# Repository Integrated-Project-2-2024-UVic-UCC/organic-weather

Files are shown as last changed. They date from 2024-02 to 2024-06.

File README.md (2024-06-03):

#  ORGANIC WEATHER STATION
The "Organic Weather Station" blends botanical aesthetics with robotics, creating a responsive flower-like robot. Equipped with photodiodes, a stepper motor, and an ESP32, this design emulates the natural behavior of flower petals that open and close with changes in light levels. It demonstrates a harmonious integration of components, providing both environmental feedback and decorative value in indoor settings.

## Features
- **Adaptive Petal Movement**:  Responds to light intensity data from photodiodes, controlling the movement of its petals to mimic natural responses.
- **Environmental Feedback**: Responds to light intensity data from photodiodes, controlling the movement of its petals to mimic natural responses.
- **Remote Weather Updates**: Connects with a Telegram chat to retrieve and display weather conditions from any specified location.
- **Ambient LED Effects**: Incorporates LEDs within the petals that shift colors based on the ambient room temperature.

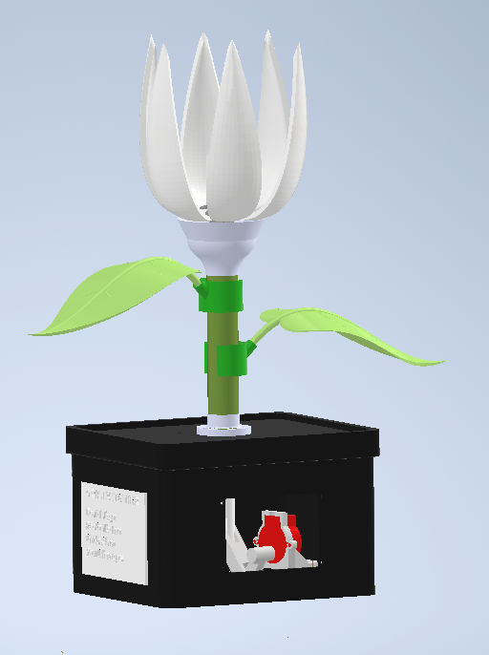
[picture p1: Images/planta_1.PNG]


If you are interested in carrying out this project, we invite you to the following sections!

## README STRUCTURE
- [Promotional Video](#promotional-video)
- [Materials](#materials)
- [Mechanical part](#mechanical-part)
    - [ 3D printed parts](#3d-printed-parts)
    - [Hardware parts](#hardware-parts)
- [Electrical Part](#electrical-part)
    - [Datasheets](#datasheets)
    - [Electric scheme](#electric-scheme)
- [Programming Part](#programming-part)

## PROMOTIONAL VIDEO
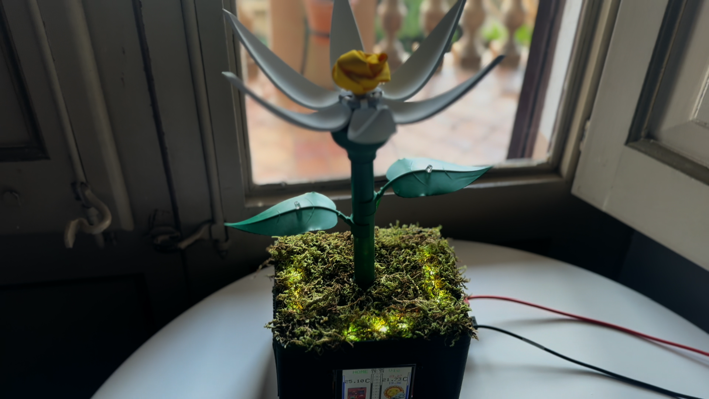
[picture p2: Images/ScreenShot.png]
Video Screenshot

[Promotional video](https://github.com/Integrated-Project-2-2024-UVic-UCC/organic-weather/blob/main/Images/OrganicWeather_PromotionalVideo.mp4)
## MATERIALS
Before starting with the mechanical part, we will show you the list of materials that have been used and the links where you can buy it:
|Component|Description|Link|Price (€)|
|---|---|---|---|
| |ESP32-DEVKITC-32UE, MAIN SHIELD |(https://www.digikey.es/es/products/detail/espressif-systems/ESP32-DEVKITC-32UE/12091813) |9,23 €|
| |TFT LCD 3.2″ 240×320 RGB SPI Display with Touchscreen| https://protosupplies.com/product/tft-lcd-3-2-240x320-rgb-spi-display-with-touchscreen/ | 17,7 €|
| |Stepper motor 28BYJ-48 (5V) with ULN2003 driver|https://tienda.bricogeek.com/motores-paso-a-paso/969-motor-paso-a-paso-28byj-48-5v-con-driver-uln2003.html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 | 2,95 €|
| | DHT22 humidity and temperature sensor| https://eu.robotshop.com/es/products/dht22-temperature-humidity-sensor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 | 7,49 €|
| | SFH 203 P Photodiode | https://www.digikey.es/es/products/detail/ams-osram-usa-inc/SFH-203-P/1893875 | 1 - 0,92 € |
| |WS2812B Module Circuit with RGB Led| https://www.shoptronica.com/led-bicolor-tricolor-rgb/3959-circuito-modulo-ws2812b-con-led-rgb-0689593949912.html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 | 1 - 0,2610 €|

The datasheets for these components can be found in the following folder: [Datasheets](https://github.com/Integrated-Project-2-2024-UVic-UCC/organic-weather/tree/main/Electronic/Datasheets)

## MECHANICAL PART
  ### 3D printed parts

After reviewing the description of the organic weather station and understanding its required functions and movements, this section will explain the mechanisms used to ensure the flowers open and close correctly each time.
Flower mechanism
As a first option, it was proposed to move the petals using four gears, each connected to a petal, and a worm gear in the center, connected to the motor. This mechanism was to allow the petals to open and close depending on the light intensity of the environment. The worm gear turned and had to engage with the gears to make them rotate, which worked in the simulation. However, when printed, the system generated too much friction, which caused constant breakage and malfunction. Because of these friction and unreliability problems, the design was eventually discarded.
After this, a new design was started. This innovative design does not have gears or worm gear, in short, it has two pieces without considering the petals. The first piece will be a central piece, one end of which will be connected to the stepper motor that will carry out the movement and the other part is where the petals will be hooked. This part will be like a crown where the petals will be placed, that is, they will fit together, allowing the petal to have complete movement. We could imagine the movement as that of a hinge. The second piece will be both functional and visual. We can see that visually it will be a calyx of a flower and inside it will have the shape of a coup. Its function will be that when the central piece lowers, the petals, when resting on the calyx, begin to close on the inside of the cup, so when the central piece has reached its minimum, the flower is completely closed. 

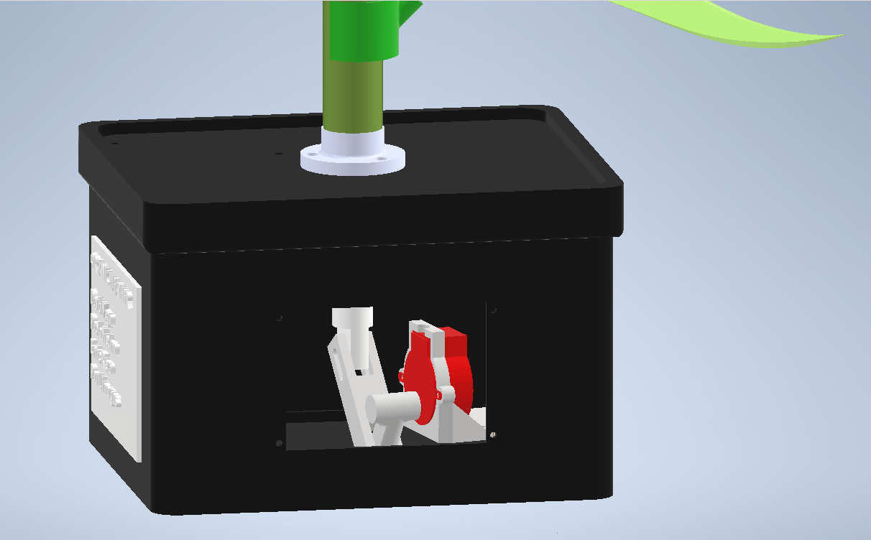
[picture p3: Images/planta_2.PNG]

|Component|Description|3D part|
|---|---|---|
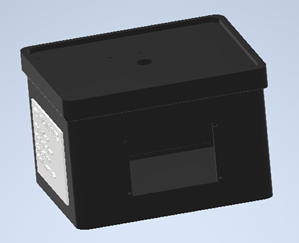
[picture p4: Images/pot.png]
| POT | Pot of the plant, inside it has all the electronic components |  |
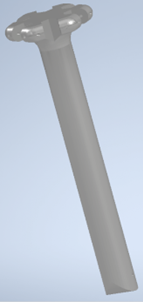
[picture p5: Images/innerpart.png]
| INNER PART | The Main bar, to move the petals of the flower, is connected to the stepper motor | |
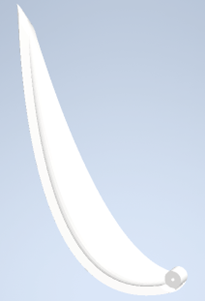
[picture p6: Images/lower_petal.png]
| FLOWER PETAL | Six of these complete the flower, with the hinge on the bottom it connects to the Inner Part, to be able to open and close |  |
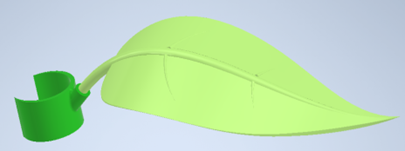
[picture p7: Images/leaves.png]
| LEAVES | The greener is the support of the leaf that it is attached to the stem of the plant. We have two, one on each side, the left and the right. |  |

These are the parts of the mechanism inside the pot, that we use:

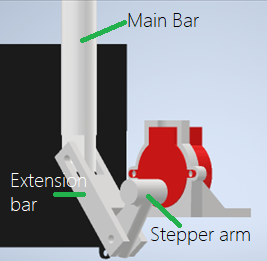
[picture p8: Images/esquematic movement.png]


  ### Hardware parts
  
## ELECTRICAL PART
  ### Datasheets
  You can find the datasheets for the following components in the [datasheets folder](https://github.com/Integrated-Project-2-2024-UVic-UCC/organic-weather/tree/main/Electronic/Datasheets):
  - ESP32
  - Photodiodes
  - LEDs RGB
  - DHT22 humidity and temperature sensor
  ### Electric scheme
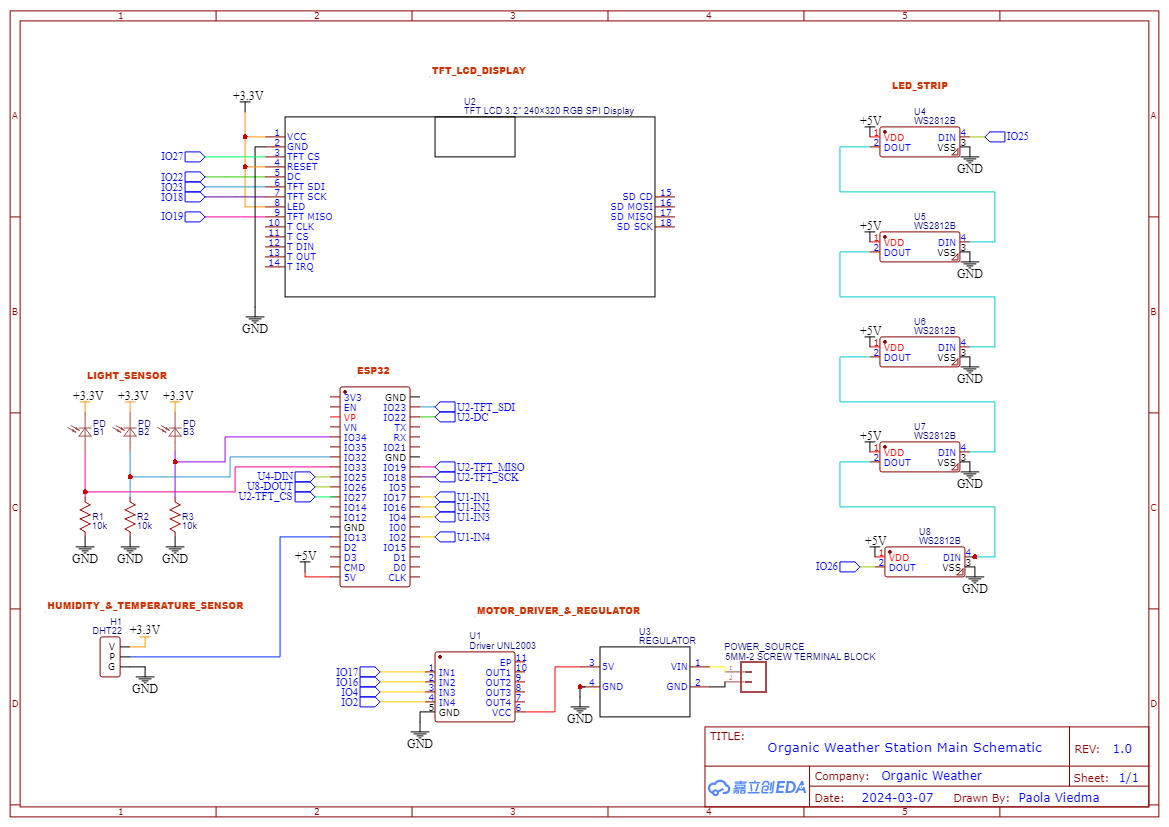
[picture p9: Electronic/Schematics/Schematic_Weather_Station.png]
Schematic_Weather_Station
  )
  [![Electric Scheme]([https://github.com/Integrated-Project-2-2024-UVic-UCC/organic-weather/blob/main/Electronic/Schematics/Schematic_Weather_Station.png](https://github.com/Integrated-Project-2-2024-UVic-UCC/organic-weather/blob/main/Electronic/Schematics/Schematic_Integrated%20Project_2024-04-24.png))](https://github.com/Integrated-Project-2-2024-UVic-UCC/organic-weather/tree/main/Electronic/Schematics)

## PROGRAMMING PART
The libraries used are located in the Code folder, as a folder called LIBRARIES. 
Here is explained synthesized the main workflow of the code. 

### Workflow of the HTTP Client 
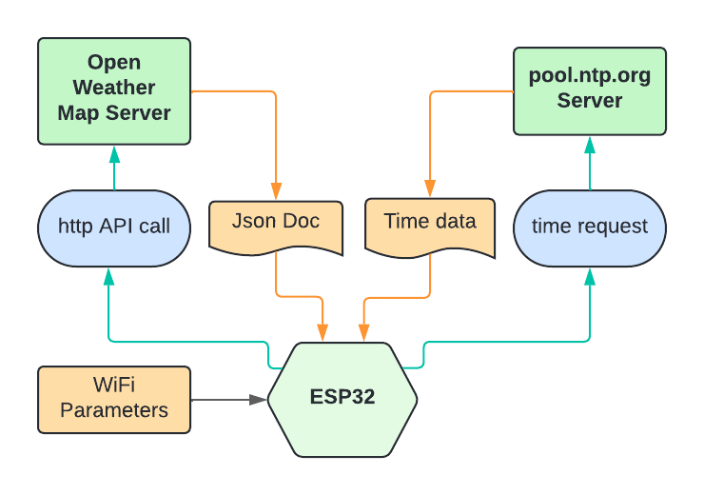
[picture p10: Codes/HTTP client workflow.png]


### Global/Loop workflow 
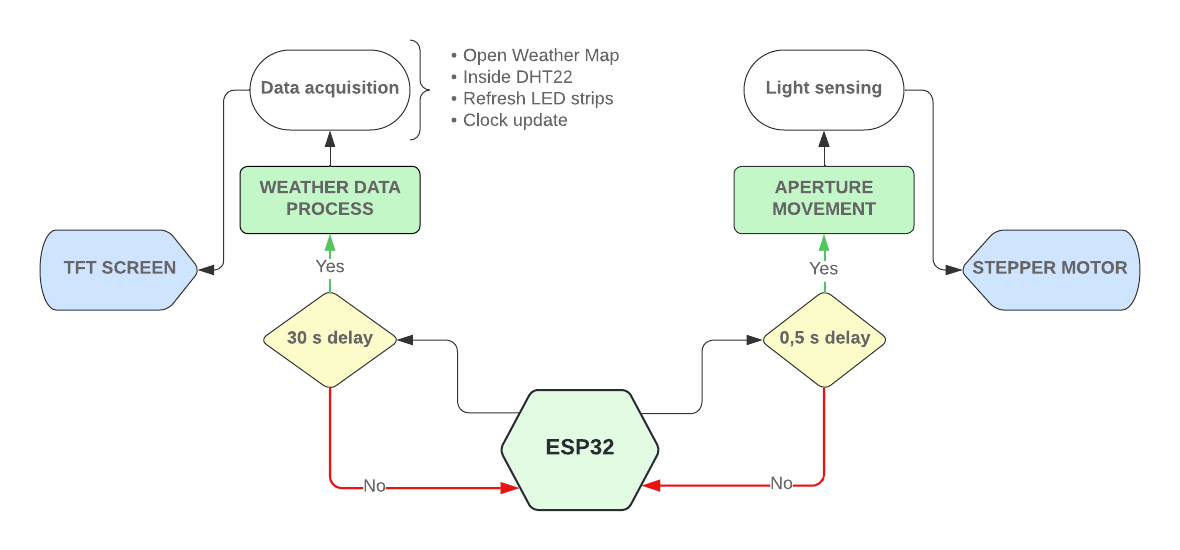
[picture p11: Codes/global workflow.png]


### Setup
For inicialize the plant:
- Starts the screen with the welcome screen
- Reset the position of the stepper motor
- Starts the WiFi connection
- Configure the Real Time Clock of the ESP32
- Do a first run of two main processes
  - Light sensing and motor position
  - Data adquire and data display

### Loop
When the system has been started up correctly, the main loop only execute two subprocesses:
- Light sensing and motor position
- Data aquire and data display
  
This two subprocesses have diferent delay time, controlled by comparison of the millis() function.
For the aperture of the leaves needs a fast frequency, is set to 0,5 seconds.
For the data aquire and data display doesn't need a high frequency because the data may not vary significantly. The delay is set to 30 seconds.

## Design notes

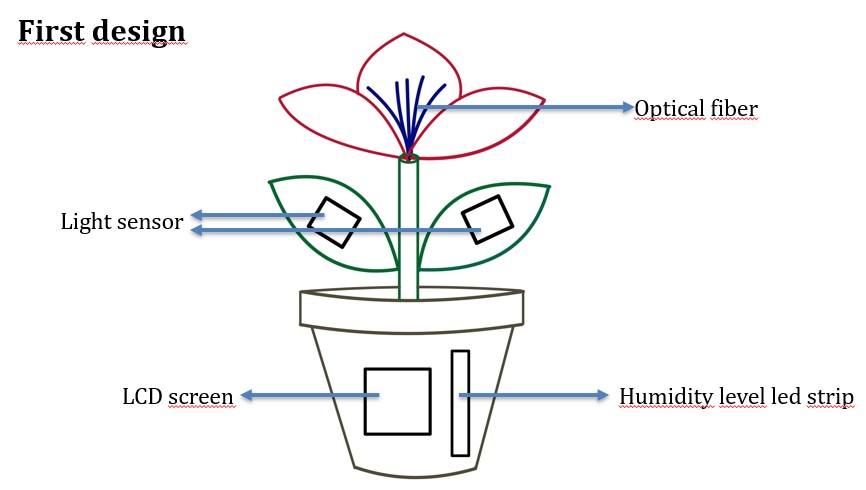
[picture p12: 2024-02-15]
Images/first_design.jpg

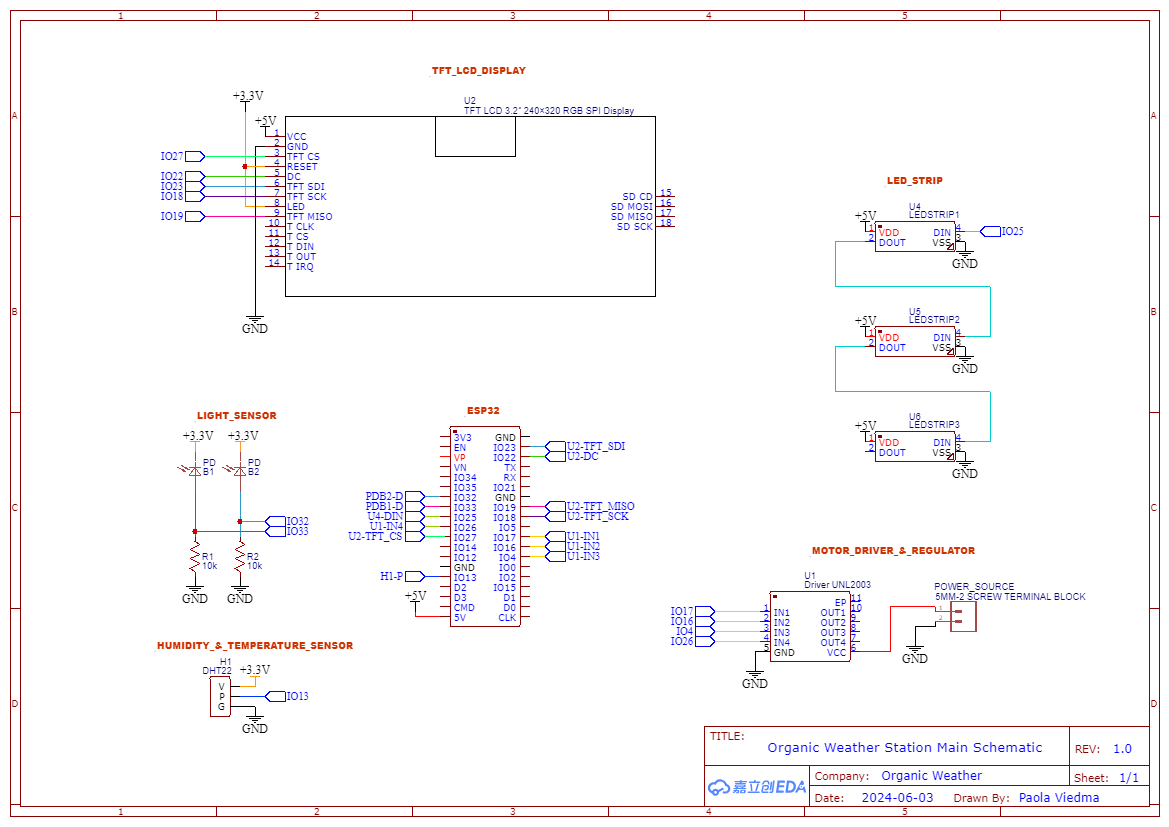
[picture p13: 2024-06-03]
Electronic/Schematics/Schematic_Integrated Project_2024-06-03.png

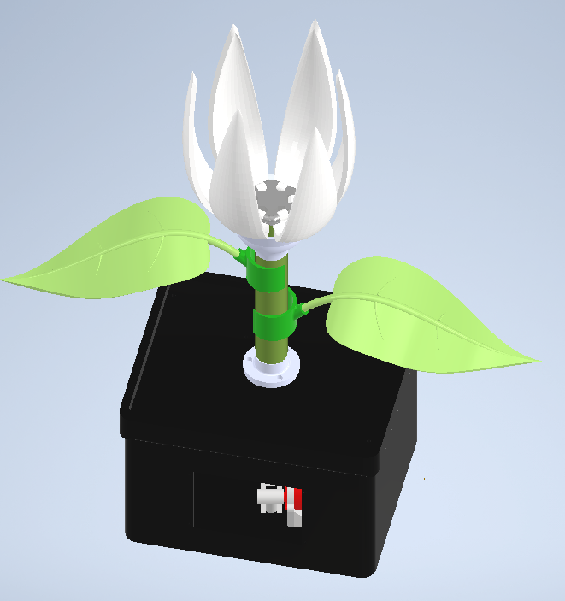
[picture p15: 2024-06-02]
Images/planta_4.PNG

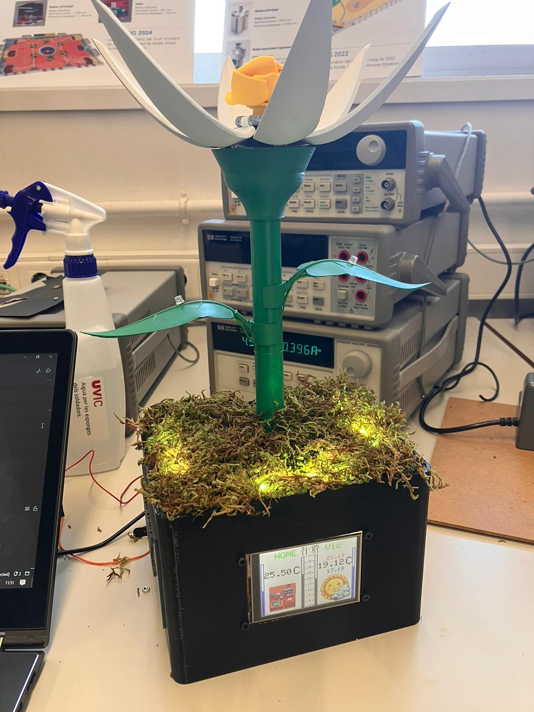
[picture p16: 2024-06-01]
Images/final_prototype.jpg

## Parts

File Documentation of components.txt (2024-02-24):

Arduino nano ble
14 I/O

The power supply will come directly from the battery, with the pins Vin and GND that supports a top of 21 V.
The converter 12V to 5V will supply the servomotor. 
It will be possible that this converter feeds the LEDs and the fiberoptic.

Outputs: 
	1 PWM servomotor control
	3 PWM for the control of the three colors of RGB LEDs termometer
	1 of tqhe fiberoptics

I2C:
	DHT22 temp and hum
	OLED Display

Inputs:
	3 analog inputs from the photoresistor

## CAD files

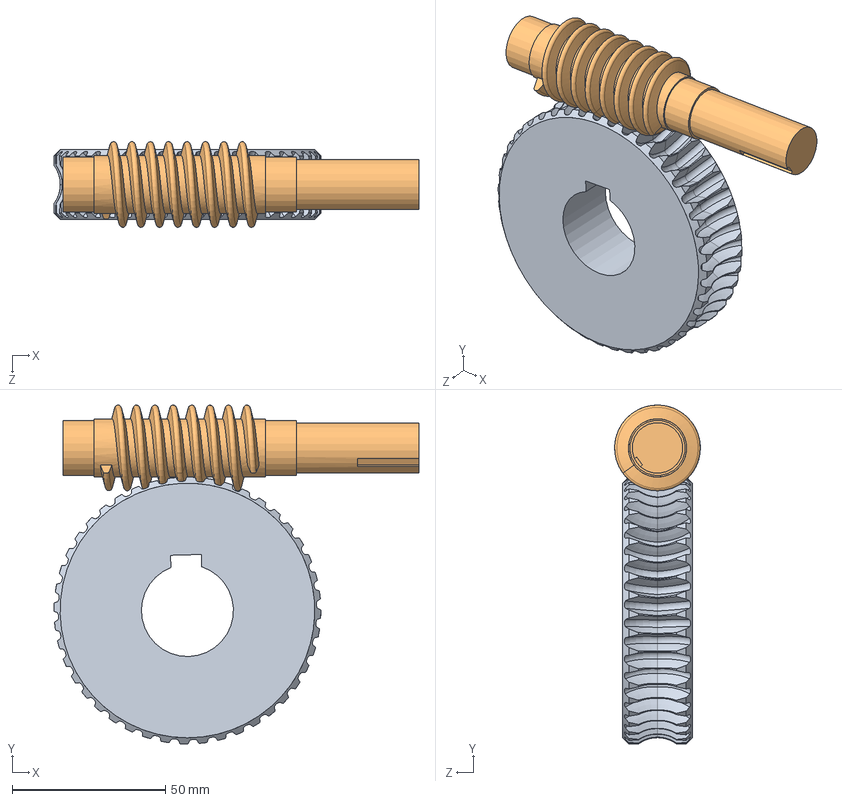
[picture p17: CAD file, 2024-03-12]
Mechanic and Desings/Diferents design (not used)/Design option_1/worm gear.SLDASM
119.0 x 110.5 x 28.0 mm
Worm gear

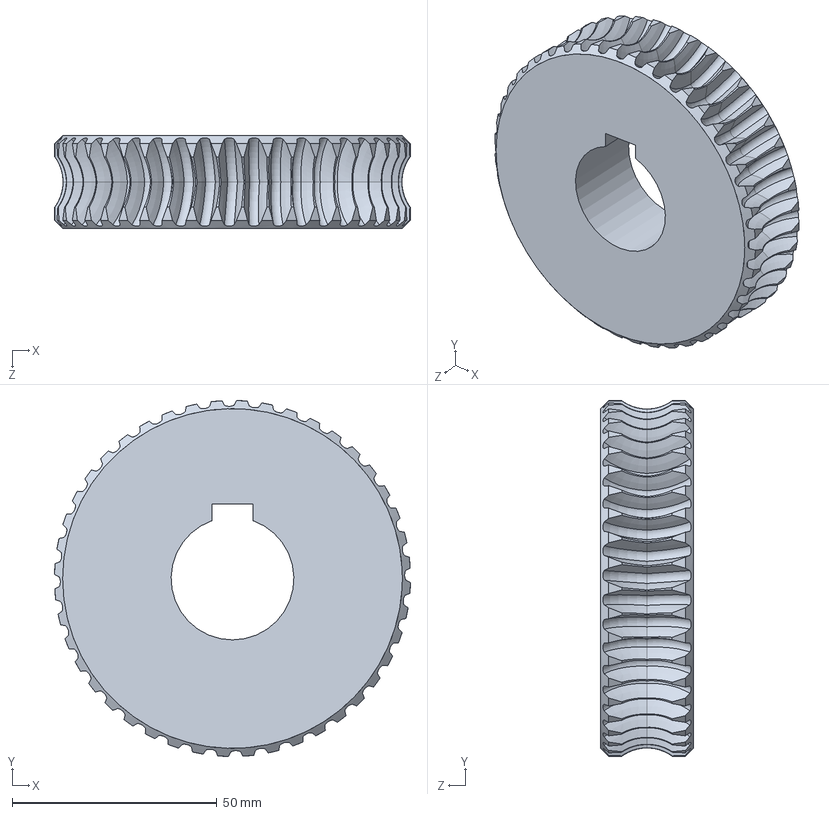
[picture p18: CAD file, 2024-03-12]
Mechanic and Desings/Diferents design (not used)/Design option_1/2.SLDPRT
87.0 x 87.0 x 22.7 mm

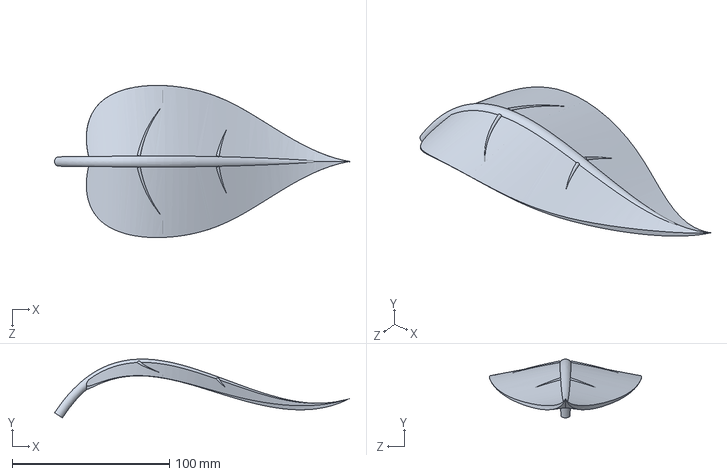
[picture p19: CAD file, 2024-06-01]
Mechanic and Desings/plant/Part1.SLDPRT
187.6 x 37.4 x 96.8 mm

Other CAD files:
Mechanic and Desings/Draw schematics/suport_fulla_plànol.dwg
Mechanic and Desings/Draw schematics/fulla_plànol.dwg
Mechanic and Desings/Diferents design (not used)/Design option_2/test_1.dwg
Mechanic and Desings/Draw schematics/extensió_plànol.dwg
Mechanic and Desings/Draw schematics/Barra_principal_planol.dwg
Mechanic and Desings/Draw schematics/suport_tija_plànol.dwg
Mechanic and Desings/Draw schematics/Tapa_test_plànol.dwg
Mechanic and Desings/Draw schematics/piu-guia_plànol.dwg
Mechanic and Desings/Draw schematics/Pètal_plànol.dwg
Mechanic and Desings/Draw schematics/Suport_stepper_plànol.dwg
Mechanic and Desings/Draw schematics/Calze_plànol.dwg
Mechanic and Desings/Draw schematics/Test_plànol.dwg
Mechanic and Desings/Draw schematics/Tapa_darrere_plànol.dwg
Mechanic and Desings/Draw schematics/cilindre_exterior_plànol.dwg
Mechanic and Desings/Draw schematics/Stepper_model_plànol.dwg
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

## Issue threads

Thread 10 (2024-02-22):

Worm-Gear Mechanism

LlimargasP, 2024-02-22:
Design of the mechanisms that we are going to use to be able to open and close the flower of the plant using a end screw and gears

davidvega2001, 2024-04-11:
The design using inventor caused some problems with the desired parameters.

Closed 2024-04-11.

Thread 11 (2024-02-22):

How the LCD display works

davidvega2001, 2024-02-22:
LCD display will show the inputs from sensors (Temperature, Humidity) and information such date and season.
Start learning the previous setup (libraries needed) and connections.
Search for examples.

davidvega2001, 2024-05-09:
The code merging the TFT control and the openweathermap data is finished correctly. For other tasks, there are some points to add or improve.

- Screen reloading, make it more fluent
- Graphical logo and states like(cloud, sunny, rain)

Closed 2024-05-09.

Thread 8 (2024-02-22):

How the stepper works

davidvega2001, 2024-02-22:
Search the libraries needed for work the servo selected. Install them, and find examples codes and start the setup of this device in the arduino IDE.

davidvega2001, 2024-02-22:
Search the libraries needed for work the servo selected. Install them, and find examples codes and start the setup of this device in the arduino IDE.

davidvega2001, 2024-04-02:
This code was succesful finished. The program only needs one parameter for do all the calculations and power on the motor in the correct direcction with the determined steps. This parameter is the angular position in turns.

Closed 2024-04-02.

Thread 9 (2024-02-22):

Electronics Schematic Draft

PViedma13, 2024-02-22:
Based on the knowledge obtained from the datasheets of all the components, we can make the first draft of the electronic board of the entire mechanism, connecting all the components.

PViedma13, 2024-02-22:
Based on the knowledge obtained from the datasheets of all the components, we can make the first draft of the electronic board of the entire mechanism, connecting all the components.

davidvega2001, 2024-04-02:
Schematic draft done.

Closed 2024-04-02.

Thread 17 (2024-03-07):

Alternative mechanism

LlimargasP, 2024-03-07:
Design of the mechanisms that we are going to use to be able to open and close the flower  if the other desing is not working properly, using a system composed of a crown grapling all the flowers and a stick attached to a servo motor

davidvega2001, 2024-04-02:
We finally refused this mechanism, due to some desing issues.

Closed 2024-04-02.

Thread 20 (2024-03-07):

Connexion between ESP32 and telegran channel

davidvega2001, 2024-03-07:
From a telegram channel, we can pull information of the weather of the city located. For later display along side our data from the organic weather station.

davidvega2001, 2024-04-02:
This task was not fully finished due to issues for the maintain the server and the API for our telegram bot.

Closed 2024-04-02.

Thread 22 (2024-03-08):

List of material received

moises-garin, 2024-03-08:
This is the list of the materials you have received. Each item will be checked-out once returned at the end of the course. All material must be returned before receiving your final maks.

**IMPORTANT** Ony the teachers must modify this issue. In case of detecting an error, you must inform the teachers inmediately.

- [ ] 20 leds indexables
- [ ] 1 mini stepper + driver ULN2003
- [ ] 1 sensor DHT22
- [ ] 1 pantalla TFT 3,5""
- [ ] 1 ESP32
- [ ] 1 proto (sense un tros lateral)

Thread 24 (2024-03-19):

3d printing prototype pieces

Enric1Vic, 2024-03-19:

Enric1Vic, 2024-03-21:
start printing the main functional pieces of the prototype

davidvega2001, 2024-04-11:
1st attempt of the worm-gear mechanism with the support for them. The reduction was of 35% form the original sketch.

Closed 2024-04-11.

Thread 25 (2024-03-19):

soldering pins

Enric1Vic, 2024-03-19:

Enric1Vic, 2024-03-21:
Soldering the rgb to the pcb

davidvega2001, 2024-04-11:
The esp can be attached to the pcb with easy connect pins soldered at one side.

Closed 2024-04-11.

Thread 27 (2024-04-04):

Luminosity sensing

davidvega2001, 2024-04-04:
Once we have the schematic of the photodiodes and the correct resistor selected, the objective of this task is to develop a code for; data acquire, proceed to modify the position of the gear and the intensity of the LEDs.

davidvega2001, 2024-04-09:
Finished as planed.

Closed 2024-04-09.

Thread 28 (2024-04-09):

Light ambient sensing

davidvega2001, 2024-04-09:
First part: Lecture the photodiode for measure the light ambient.

Second part: To control the aperture of the leaves, stepper motor, depending of the available light in the ambient.

davidvega2001, 2024-04-11:
The data acquired form the photodiode controlls de aperture of the leafes, with the stepper motor.

Closed 2024-04-11.

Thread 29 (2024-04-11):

3D Printing the final mechanism

davidvega2001, 2024-04-11:
Prove the printed mechanism, search issues and correct them. Try and find out the correct size.

Enric1Vic, 2024-05-02:
We decided to discard the actual mechanism (worm-gear) due to assembly problems

Closed 2024-05-02.

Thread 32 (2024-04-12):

Unify all the software features in one functionally code

davidvega2001, 2024-04-12:
Once we have the different features of the software part, like:

- stepper motor
- light sensor
- screen display
- city forecast
- temperature and humidity

The final code will be all theese unified in one, it should be checked that all functions work properly.
Also it will be excelent to improve some aspects like, wifi credentials configuration, more attractive display, etc.

davidvega2001, 2024-06-01:
The final code work properly and meets the mention objectives plus some addons like the RGB strips.

Closed 2024-06-01.

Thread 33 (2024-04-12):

Mount the base

davidvega2001, 2024-04-12:
Once we have the 3d printed parts of the base, the gear support, the gears, mount all together and install the electronic stuff.

Closed 2024-06-02.

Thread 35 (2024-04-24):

Alternative design for flower movement

PViedma13, 2024-04-24:
Because the gear system with the worm screw is not producing the results it should, it has been decided to start designing an alternative system and for now parallel to the current design:
- Parallel: because we want to do some last tests before completely discarding the current design.
- Alternative: this design does not have gears or worm screw, in short we have two pieces without taking into account the petals.
The first piece will be a central piece, one end of which will be connected to the stepper motor that will carry out the movement and the other part is where the petals will be hooked. This part will be like a crown where the petals will be placed, that is, they will fit together, allowing the petal to have complete movement. We could imagine the movement as that of a hinge. The shape is not defined.
The second piece will be both functional and visual. We can see that visually it will be a calyx of a flower and inside it will have the shape of a coap. Its function will be that when the central piece lowers, the petals, when resting on the calyx, begin to close on the inside of the cup, so when the central piece has reached its minimum, the flower is completely closed.

Visual scheme:

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

Enric1Vic, 2024-05-02:
Main stick and petals done. Working by now. Will increase the scale to fit better every piece.

Closed 2024-06-02.

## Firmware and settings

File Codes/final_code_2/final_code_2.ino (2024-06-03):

//_____________________________________________________________________________LIBRARIES 1438557
#include "SPI.h"                //Serial Peripheral Interface Bus
//#include "Adafruit_GFX.h"       //
#include "Adafruit_ILI9341.h"   //Controller of the screen
#include "WiFi.h"               //WiFi capability of the ESP32
#include "HTTPClient.h"         //For do request at servers
#include "ArduinoJson.h"        //For deserialize a json file
#include "DHT.h"                //Temperature sensor
#include "ESP32Time.h"          //To update the internal clock
#include "Adafruit_NeoPixel.h"  //LED RGB strips
#ifdef __AVR__          
 #include <avr/power.h> // Required for 16 MHz Adafruit Trinket
#endif
//*****************************************************************************END



//_____________________________________________________________________________IMAGES AND LOGOS
#include "logo.h"
#include "sun.h"
#include "suncloud.h"
#include "rain.h"
#include "snow.h"
#include "thunder.h"
//#include "mist.h"
#include "cozy.h"
//******************************************************************************END



//_____________________________________________________________________________OTHER VARIABLES
float humidity, temperature, main_temp, temp_max, temp_min;
float temperature_prev, humidity_prev, main_temp_prev, temp_max_prev, temp_min_prev;
String date_prev; String time_prev; String sky;
const char*city;
int humidity_city, humidity_city_prev;

//float lat = 41.9301200, lon = 2.2548600; //not used as variable

//counter of millis
unsigned long previous_millis_step = 0; 
unsigned long previous_millis_screen = 0; 

//interval between refresh the steps or the screen
unsigned int interval_step = 500;
unsigned int interval_screen = 30000;

//*****************************************************************************END



//_____________________________________________________________________________OBJECTS
#define dht_pin 13
DHT dht(dht_pin, DHT22);
ESP32Time rtc; //real time clock
//*****************************************************************************END



//_____________________________________________________________________________PHOTODIODE
#define pd_1 34
#define pd_2 32
int luminosity, luminosity_prev = 0, luminosity_current;

void get_luminosity(){
  luminosity_prev = luminosity;
  luminosity_current = ( analogRead(pd_1)  + analogRead(pd_2)) / 2;
  luminosity = 0.5*luminosity_prev + 0.5*luminosity_current;
}
//*****************************************************************************END



//_____________________________________________________________________________TFT ILI9341
#define TFT_DC 22
#define TFT_CS 27
#define TFT_MOSI 23
#define TFT_CLK 18
#define TFT_RST 12
#define TFT_MISO 19

Adafruit_ILI9341 tft = Adafruit_ILI9341(TFT_CS, TFT_DC, TFT_MOSI, TFT_CLK, TFT_RST, TFT_MISO);

void initLCD(){
  tft.begin();
  tft.setRotation(3);
  yield();
  tft.fillScreen(ILI9341_WHITE);
  yield();
  welcome_screen();
}

void draw_box(int y0, int yf, int x0, int amplitude){
  tft.setTextSize(1);
  for(int y = y0; y<=yf; y++){ //VERTICAL LEFT
    tft.setCursor(x0,y);   tft.println(".");
  }
  for(int y = y0; y<=yf; y++){ //VERTICAL RIGHT
    tft.setCursor(x0+amplitude,y);  tft.println(".");
  }
  for(int x = x0; x<=x0+amplitude; x++){ //up fill
    tft.setCursor(x,y0);  tft.println(".");
  }
  for(int x = x0; x<=x0+amplitude; x++){ //down fill
    tft.setCursor(x,yf);  tft.println(".");
  }
}

void refill_box(float var, int y0, int yf, int x0, int amplitude){
  tft.setTextSize(1);
  for(int y = (100-var)*(yf-y0)/100+y0; y<yf; y++) {
    for(int x = x0+3; x<=x0+amplitude-3; x++){
    tft.setCursor(x,y); tft.println(".");
    }
  }
}

void refill_temp_box(float var, int y0, int yf, int x0, int amplitude){
  tft.setTextSize(1);
  for(int y = map(var,-5,40,195,0)+y0; y<yf; y++) {
    for(int x = x0+3; x<=x0+amplitude-3; x++){
    tft.setCursor(x,y); tft.println(".");
    }
  }
} 

unsigned long welcome_screen() {
  unsigned long start;
  tft.drawRGBBitmap(0,0,(uint16_t *)logoBitmap, LOGO_WIDTH, LOGO_HEIGHT);
  return micros() - start;
}

unsigned long background_screen(){
  unsigned long start;
  tft.fillScreen(ILI9341_WHITE);

  tft.setTextColor(ILI9341_GREEN); tft.setTextSize(3); tft.setCursor(35+15,10); tft.println("HOME");//____________HOME TITLE

  if(WiFi.status() == WL_CONNECTED){
    tft.setTextColor(ILI9341_GREEN); tft.setTextSize(3); tft.setCursor(160+35+20,10); tft.println(city);//________CITY TITLE
  } 
  
  tft.setTextColor(ILI9341_BLUE);
  draw_box(35, 230, 2, 8); //___________________HUMIDITY INSIDE BOX
  draw_box(35, 230, 320-8-2-6, 8); //___________HUMIDITY CITY BOX

  tft.setTextColor(ILI9341_BLACK);
  draw_box(35, 230, 320/2-10-2-15, 8); //_______TEMP LEVEL INSIDE
  draw_box(35, 230, 320/2+2+15, 8); //___________TEMP LEVEL CITY

  tft.setTextColor(ILI9341_BLACK);
  draw_box(35, 35, 320/2-10-2-15+2+8+3, 3);                                    draw_box(35, 35, 320/2+2+15-4-3, 3);                                   //40
  draw_box(((230-35)*40/45+35), ((230-35)*5/45+35), 320/2-10-2-15+2+8+3, 3);   draw_box(((230-35)*40/45+35), ((230-35)*5/45+35), 320/2+2+15-4-3, 3);  //35
  draw_box(((230-35)*40/45+35), ((230-35)*10/45+35), 320/2-10-2-15+2+8+3, 3);  draw_box(((230-35)*40/45+35), ((230-35)*10/45+35), 320/2+2+15-4-3, 3); //30 
  draw_box(((230-35)*40/45+35), ((230-35)*15/45+35), 320/2-10-2-15+2+8+3, 3);  draw_box(((230-35)*40/45+35), ((230-35)*15/45+35), 320/2+2+15-4-3, 3); //25  
  draw_box(((230-35)*40/45+35), ((230-35)*20/45+35), 320/2-10-2-15+2+8+3, 3);  draw_box(((230-35)*40/45+35), ((230-35)*20/45+35), 320/2+2+15-4-3, 3); //20  
  draw_box(((230-35)*40/45+35), ((230-35)*25/45+35), 320/2-10-2-15+2+8+3, 3);  draw_box(((230-35)*40/45+35), ((230-35)*25/45+35), 320/2+2+15-4-3, 3); //15  
  draw_box(((230-35)*40/45+35), ((230-35)*30/45+35), 320/2-10-2-15+2+8+3, 3);  draw_box(((230-35)*40/45+35), ((230-35)*30/45+35), 320/2+2+15-4-3, 3); //10  
  draw_box(((230-35)*40/45+35), ((230-35)*35/45+35), 320/2-10-2-15+2+8+3, 3);  draw_box(((230-35)*40/45+35), ((230-35)*35/45+35), 320/2+2+15-4-3, 3); //5
  draw_box(((230-35)*40/45+35), ((230-35)*40/45+35), 320/2-10-2-15+2+8+3, 3);  draw_box(((230-35)*40/45+35), ((230-35)*40/45+35), 320/2+2+15-4-3, 3); //0
  draw_box(230-1, 230-1, 320/2-10-2-15+2+8+3, 3);                              draw_box(230-1, 230-1, 320/2+2+15-4-3, 3);                             //-5
  
  tft.setTextColor(ILI9341_RED);   tft.setTextSize(1.9); tft.setCursor(320/2-3,35+2); tft.println(40);
  tft.setTextColor(ILI9341_BLACK); tft.setTextSize(1.9); tft.setCursor(320/2-3,((230-35)*5/45+35)+2); tft.println(35);
  tft.setTextColor(ILI9341_BLACK); tft.setTextSize(1.9); tft.setCursor(320/2-3,((230-35)*10/45+35)+2); tft.println(30);
  tft.setTextColor(ILI9341_BLACK); tft.setTextSize(1.9); tft.setCursor(320/2-3,((230-35)*15/45+35)+2); tft.println(25);
  tft.setTextColor(ILI9341_BLACK); tft.setTextSize(1.9); tft.setCursor(320/2-3,((230-35)*20/45+35)+2); tft.println(20);
  tft.setTextColor(ILI9341_BLACK); tft.setTextSize(1.9); tft.setCursor(320/2-3,((230-35)*25/45+35)+2); tft.println(15);
  tft.setTextColor(ILI9341_BLACK); tft.setTextSize(1.9); tft.setCursor(320/2-3,((230-35)*30/45+35)+2); tft.println(10);
  tft.setTextColor(ILI9341_BLACK); tft.setTextSize(1.9); tft.setCursor(320/2,((230-35)*35/45+35)+2); tft.println(5);
  tft.setTextColor(ILI9341_BLACK); tft.setTextSize(1.9); tft.setCursor(320/2,((230-35)*40/45+35)+2); tft.println(0);
  tft.setTextColor(ILI9341_BLUE);  tft.setTextSize(1.9); tft.setCursor(320/2-4,230-1+2); tft.println(-5);

  tft.drawRGBBitmap(2+8+8,240/2+5,(uint16_t *)cozyBitmap, IM_WIDTH, IM_HEIGHT);

  return micros() - start;
}

unsigned long data_screen() {
  unsigned long start;
  int xtemp=95; int ytemp=210/2-30;

  tft.setTextColor(ILI9341_WHITE); tft.setTextSize(2); tft.setCursor(320/2-25, 5); tft.println(date_prev); // CLEAN DATE
  tft.setTextColor(ILI9341_BLACK); tft.setTextSize(2); tft.setCursor(320/2-25, 5); tft.println(rtc.getTime("%d/%m")); //DATE
  
  tft.setTextColor(ILI9341_WHITE); tft.setTextSize(2); tft.setCursor(320/2-25, 20); tft.println(time_prev); //CLEAN TIME
  tft.setTextColor(ILI9341_BLACK); tft.setTextSize(2); tft.setCursor(320/2-25, 20); tft.println(rtc.getTime("%H:%M")); //TIME

  //________________________________________________________________TEMPERATURE
  tft.setTextColor(ILI9341_WHITE); tft.setTextSize(3.7);  tft.setCursor(15,ytemp);          tft.println(temperature_prev);
  tft.setTextColor(ILI9341_BLACK); tft.setTextSize(3.7);  tft.setCursor(15,ytemp);          tft.println(temperature);
  tft.setTextColor(ILI9341_BLACK); tft.setTextSize(4);    tft.setCursor(15+xtemp,ytemp-3);  tft.println("C");

  //________________________________________________________________TEMPERATURE LEVEL
  tft.setTextColor(ILI9341_WHITE); refill_temp_box(temperature_prev, 35,  230, 320/2-10-2-15, 8);
  tft.setTextColor(ILI9341_BLACK); refill_temp_box(temperature, 35,  230, 320/2-10-2-15, 8);

  //________________________________________________________________HUMIDITY INSIDE LEVEL
  tft.setTextColor(ILI9341_WHITE);  refill_box(humidity_prev, 35, 230, 2, 8); //CLEAN REFILL
  tft.setTextColor(ILI9341_BLUE);   refill_box(humidity, 35, 230, 2, 8);//REFILL 




  //_/_/_/_/_/_/_/_/_/_/_/_/_/_/_/_/_/_/_/_/_/_/_/_/_/_/_/_/_/_/_/_/_/_/_/_/_/_/_/_/_/_/_/_/_/_/_/_/_/_/_/_/_/_/_/_/_/_/_/_/_/_/_/_/_/_/_____CITY
  if(WiFi.status() == WL_CONNECTED){
    //tft.setTextColor(ILI9341_WHITE); tft.setTextSize(3.7);
    //tft.setCursor(160+50,220/2);  tft.println("NO");  tft.setCursor(160+50,220/2+30);  tft.println("DATA");

    tft.setTextColor(ILI9341_GREEN); tft.setTextSize(3); tft.setCursor(160+35+20,10); tft.println(city);//________CITY TITLE
    
    tft.setTextColor(ILI9341_WHITE);  refill_box(humidity_city_prev, 35, 230, 320-8-2-6, 8); //_____CLEAN HUMIDITY CITY
    tft.setTextColor(ILI9341_BLUE);   refill_box(humidity_city, 35, 230, 320-8-2-6, 8); //__________REFILL WITH HUMIDITY CITY


    //_____________________________________________________________MAIN TEMPERATURE
    tft.setTextColor(ILI9341_WHITE); tft.setTextSize(3.7); tft.setCursor(160+30,ytemp); tft.println(main_temp_prev);
    tft.setTextColor(ILI9341_BLACK); tft.setTextSize(3.7); tft.setCursor(160+30,ytemp); tft.println(main_temp);
    
    tft.setTextColor(ILI9341_BLACK); tft.setTextSize(4);  tft.setCursor(160+30+xtemp,ytemp-3);  tft.println("C");

    //________________________________________________________________TEMPERATURE CITY LEVEL
    tft.setTextColor(ILI9341_WHITE); refill_temp_box(main_temp_prev, 35,  230, 320/2+2+15, 8);
    tft.setTextColor(ILI9341_BLACK); refill_temp_box(main_temp, 35,  230, 320/2+2+15, 8);

    //_____________________________________________________________MAX AND MIN TEMPERATURE
    tft.setTextColor(ILI9341_WHITE); tft.setTextSize(2.5);  tft.setCursor(160+60,ytemp-20);  tft.println(temp_max_prev);
    tft.setTextColor(ILI9341_RED); tft.setTextSize(2.5);  tft.setCursor(160+60,ytemp-20);  tft.println(temp_max);

    tft.setTextColor(ILI9341_WHITE); tft.setTextSize(2.5); tft.setCursor(160+60,ytemp+30);  tft.println(temp_min_prev);
    tft.setTextColor(ILI9341_BLUE); tft.setTextSize(2.5); tft.setCursor(160+60,ytemp+30);  tft.println(temp_min);

    //___________________________PICTURE SELECTION
    if(sky == "broken clouds" or sky == "scattered clouds" or sky == "few clouds" or sky == "overcast clouds"){
      tft.drawRGBBitmap(320/2+2+15+8+10,240/2+5,(uint16_t *)suncloudBitmap, IM_WIDTH, IM_HEIGHT);
    }else if(sky == "clear sky"){
      tft.drawRGBBitmap(320/2+2+15+8+10,240/2+5,(uint16_t *)sunBitmap, IM_WIDTH, IM_HEIGHT);
    }else if(sky == "shower rain" or sky == "rain"){
      tft.drawRGBBitmap(320/2+2+15+8+10,240/2+5,(uint16_t *)rainBitmap, IM_WIDTH, IM_HEIGHT);
    }else if(sky == "thunderstorm"){
      tft.drawRGBBitmap(320/2+2+15+8+10,240/2+5,(uint16_t *)thunderBitmap, IM_WIDTH, IM_HEIGHT);
    }else if(sky == "snow"){
      tft.drawRGBBitmap(320/2+2+15+8+10,240/2+5,(uint16_t *)snowBitmap, IM_WIDTH, IM_HEIGHT);
    }else if(sky == "mist"){
      tft.drawRGBBitmap(320/2+2+15+8+10,240/2+5,(uint16_t *)suncloudBitmap, IM_WIDTH, IM_HEIGHT); 
    }

  }
  return micros() - start;
} 
//*****************************************************************************END 



//_____________________________________________________________________________STEPPER AND DRIVER
#define IN1  17
#define IN2  16
#define IN3  4
#define IN4  26

int current_step = 0; //tells the current position in steps referenced at the 0º at the start
int steps;              //steps needed to achieve the rev_pos, could be negative
int t = 0;
char period = 25;          // ms for ajust the speed

int step_eq [5][4] = { //for more torque needed, could be used when lifting weight
  {1, 1, 0, 0},
  {0, 1, 1, 0},
  {0, 0, 1, 1},
  {1, 0, 0, 1},
  {0, 0, 0, 0}
};

void position(int rev_pos){
  //calculate the steps needed to do, in reference to the actual position
  steps = 0;
  t = 0;
  steps = rev_pos * 2.0480 - current_step;
  steps = round(steps);

  if(steps>0){ //___________________________________counter clock wise - positive___________________________________
    while(t < steps){
      for (char i = 0; i < 4; i++){
        digitalWrite(IN1, step_eq[i][0]);
        digitalWrite(IN2, step_eq[i][1]);
        digitalWrite(IN3, step_eq[i][2]);
        digitalWrite(IN4, step_eq[i][3]);
        delay(period);
        t++;
      }
    }    
  }


  if(steps<0){ //______________________________________clock wise - negative______________________________________
    while(t > steps){ //steps is a negative value
      for (char i = 3; i>=0; i--){
        digitalWrite(IN1, step_eq[i][0]);
        digitalWrite(IN2, step_eq[i][1]);
        digitalWrite(IN3, step_eq[i][2]);
        digitalWrite(IN4, step_eq[i][3]);
        delay(period);
        t--;
      }
    }

  }
  current_step+=t;
  //turn of all the bobines
  digitalWrite(IN1, step_eq[4][0]);
  digitalWrite(IN2, step_eq[4][1]);
  digitalWrite(IN3, step_eq[4][2]);
  digitalWrite(IN4, step_eq[4][3]); 
}
//*****************************************************************************END



//_____________________________________________________________________________WiFi 
const char* ssid = "organic";
const char* password = "organicweather";
void initWiFi(){
  char w = 0;
  WiFi.mode(WIFI_STA); //set the esp to a wifi station
  WiFi.begin(ssid, password);
  while(WiFi.status() != WL_CONNECTED){
    if(w >=5){
      w=0;
      break;
    }
    w++;
    delay(1000);
  }
  w=0;
}
//*****************************************************************************END 



//_____________________________________________________________________________OPEN WEATHER MAP
void visualizeJson(String input) { //input payload, the answer of the openweather
  StaticJsonDocument<1024> doc; //reserve 1024 bytes

  //doc stores the json, doc is the root
  DeserializationError error = deserializeJson(doc, input);

  //if (error){ //if it can not deserialize the 'input'
    //Serial.print("deserializeJson() failsed: ");
    //Serial.println(error.c_str());
  //  return;
  //} 

  const char* city_in = doc["name"];
  city = city_in;

  JsonObject main = doc["main"];
  JsonObject weather = doc["weather"][0];

  float main_temp_in = main["temp"];
  main_temp = main_temp_in;

  float temp_min_in = main["temp_min"];
  temp_min = temp_min_in;

  float temp_max_in = main["temp_max"];
  temp_max = temp_max_in;

  int humidity_in = main["humidity"];
  humidity_city = humidity_in;

  String sky_in = weather["description"];
  sky = sky_in;
}

String getOpenWeatherData(){ //the function that returns a String that do the API call.
  String result = "";
  HTTPClient http; 
  http.begin( //
    "https://api.openweathermap.org/data/2.5/weather" \
    "?lat=41.9301200&lon=2.2548600" \ 
    "&units=metric&lang=en" \
    "&appid=179f9a1a184ba4f7ba08aecf2b281bca");

    int httpCode = http.GET();
    if (httpCode == HTTP_CODE_OK){
      result = http.getString();
    }
    http.end(); //ends the comunication of http
    return result;
}
//*****************************************************************************END



//_____________________________________________________________________________LED RGB
char R, G, B;
Adafruit_NeoPixel pixels = Adafruit_NeoPixel(12, 25, NEO_GRB + NEO_KHZ800);
void update_RGB(){
  if(temperature>=-5.0 & temperature<0.0){ //-5 (255,20,147)
    R = map(temperature,-5.0,0,255,100);
    G = map(temperature,-5.0,0,20,0);
    B = map(temperature,-5.0,0,147,255);
  }else if(temperature>=0.0 & temperature<10.0){ //0 (50,0,255)
    R = map(temperature,0.0,10.0,50,0);
  }else if(temperature>=10.0 & temperature<20.0){ //10 (0,255,128)
    G = map(temperature,0.0,10.0,0,255);
    B = map(temperature,0.0,10.0,255,128);    
    R = map(temperature,10.0,20.0,0,128);
    G = map(temperature,10.0,20.0,255,255);
    B = map(temperature,10.0,20.0,128,0); 
  }else if(temperature>=20.0 & temperature<30.0){ //20 (128,255,0)
    R = map(temperature,20.0,30.0,128,255);
    G = map(temperature,20.0,30.0,255,128);
    B = map(temperature,20.0,30.0,0,0);    
  }else if(temperature>=30.0 & temperature<=40.0){ //30 (255,128,0)
    R = map(temperature,30.0,40.0,255,255);
    G = map(temperature,30.0,40.0,128,0);
    B = map(temperature,30.0,40.0,0,0);            //40 (255,0,0)
  }else{
    R = 255;  G = 255;  B = 255;
  }
}
//*****************************************************************************END



//_____________________________________________________________________________DATA TREATMENT
void data_acquire(){
  temperature = dht.readTemperature();
  humidity = dht.readHumidity();

  update_RGB();
  for(char n = 0; n <= 11; n++){
    pixels.setPixelColor(n,R,G,B);
  }
  pixels.show(); 

  if (WiFi.status() == WL_CONNECTED) {
    String payload = getOpenWeatherData();
    //Serial.print(payload);
    visualizeJson(payload);
  }
}

void data_prev_reload(){

  temperature_prev = temperature;
  humidity_prev = humidity;
  main_temp_prev = main_temp;
  temp_max_prev = temp_max;
  temp_min_prev = temp_min;
  humidity_city_prev = humidity_city;
  date_prev = rtc.getTime("%d/%m");
  time_prev = rtc.getTime("%H:%M");
}
//*****************************************************************************END



void setup() {
  //Serial.begin(115200);

  //_________RGB to green for welcome
  pixels.begin();
  for(char n = 0; n <= 11; n++){
    pixels.setPixelColor(n,0,255,0);
  }
  pixels.show();
  
  initLCD();

  initWiFi();

  configTime(2*3600, 0, "pool.ntp.org");
  struct tm timeinfo;
  if(getLocalTime(&timeinfo)){
    rtc.setTimeStruct(timeinfo);
  }

  dht.begin();

  //for secure the position of the motor. Starts at closed, 0 light
  pinMode(IN1, OUTPUT);  
  pinMode(IN2, OUTPUT);  
  pinMode(IN3, OUTPUT);  
  pinMode(IN4, OUTPUT);
  position(-145); 
  current_step = 0.0;

  //Serial.println(rtc.getTime("%d/%m/%Y %H:%M:%S"));

  //first data sreen
  if(WiFi.status() != WL_CONNECTED){
    initWiFi();
  }
  data_acquire();
  background_screen();
  data_screen();
  data_prev_reload();

  get_luminosity();
  position(map(luminosity, 0, 4095, 0, 145));
}

void loop() {
  unsigned long current_millis = millis();

  if((unsigned long)(current_millis - previous_millis_step) >= interval_step){

    get_luminosity();
    position(map(luminosity,0, 4095, 0, 145));

    previous_millis_step = millis();
  }
  
  if((unsigned long)(current_millis - previous_millis_screen) >= interval_screen){

    if(WiFi.status() != WL_CONNECTED){
      initWiFi();
    }
    rtc.getTime("%d/%m/%Y %H:%M:%S");
    data_acquire();
    data_screen();
    data_prev_reload();

    previous_millis_screen = millis();
  }
  delay(500);
}

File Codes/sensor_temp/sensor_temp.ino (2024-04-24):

#include "DHT.h"
#define DHTPIN 4
#define DHTTYPE DHT22
 

DHT dht(DHTPIN, DHTTYPE);

int LED_BUILTIN = 2;
int valor;
long temperatura;

/*bool marca = 0;

void IRAM_ATTR isr() {
  marca=!marca;
  delay(100);
  Serial.print(marca);
 }
 */
  
void setup() {
Serial.begin(9600);
Serial.println(F("Sensor DHT22 test!"));
pinMode(LED_BUILTIN, OUTPUT);
dht.begin();
}

void loop() {
delay(500); //Delay per donar temps de reacció al sensor
float h = dht.readHumidity();
float t = dht.readTemperature();
valor=map(h,25,100,250,3000);

/*if (isnan(h) || isnan(t)) {
Serial.println(F("Failed to read from DHT sensor!"));
return;
}
*/

Serial.print(F("Humitat: "));
Serial.print(h);
Serial.print(F("% Temperatura: "));
Serial.print(t);
Serial.println(F("°C "));
Serial.println(valor);

digitalWrite(LED_BUILTIN, HIGH);   // turn the LED on (HIGH is the voltage level)
delay(valor);                       // wait for a second
digitalWrite(LED_BUILTIN, LOW);    // turn the LED off by making the voltage LOW
delay(valor);                       // wait for a second

}

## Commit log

2024-03-05 Testing the stepper
2024-03-12 Option 1 for the mechanism
    First option to open and close the flowers of the plant
    [2.SLDPRT, Worm gear.SLDPRT, worm gear.SLDASM]
2024-03-12 Change name of the folder to be more specific
    [2.SLDPRT, Worm gear.SLDPRT, worm gear.SLDASM]
2024-03-12 First Schematic Draft
    First schematic design of all the components without taking into account the RGB LEDs. Components used:
    - ESP32
    -TFT
    - Photodiodes
    - Motor drivers
    - Regulator
2024-03-14 Gear option 2
    [tija_suport.ipt]
2024-03-15 Datasheets and Schematic Drawing
    New pinout of the ESP32, much clearer and more informative.
    Datasheet of the board to which the RGB LEDs are connected.
    Modifications to the electrical diagram, quite definitive:
    - Change of the drawing of the ESP32, now the correct one.
    - Changed the motor driver pins, since one was connected in the boot.
    - The LED strip has been added, 5 LEDs specifically, which will go to the petals.
2024-03-19 Turn off the motor after use functionality
2024-04-04 codi temperatura
2024-04-04 Changes on the design of the CAD
2024-04-09 Correct light sensor schematic
    It has been modified the light sensor part by switching the resistor and the diode, also the polarity of the diode. This is for the accuracity by detecting the light.
2024-04-09 Codes for light sensing and control of stepper
2024-04-24 New pin added
    The TFT_CS pin was assigned to pin 27 of the ESP32 board because it is necessary to program the display.
2024-04-24 New pin added
    The TFT_CS pin of the LCD Screen has been added to pin 27 associated with the ESP32, because it is necessary for its programming
2024-05-02 New changes on the CAD Pot
    [Part1.SLDPRT]
2024-05-02 Changes on folders
    [2.SLDPRT, Worm gear.SLDPRT, engranatge_final_3.ipt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]
2024-05-02 Change on the support of the servomotor
2024-05-03 Added all libraries used in arduino
2024-05-14 Improve
    Refresh of the data improves
    Temperature level finished
    Added some sky images
2024-06-01 Definitive schematic
    Changed elements for the final design
2024-06-01 STLS
    Stl's of the calyx and the final plant stem support.
2024-06-02 Add a new final code
    The second revision is not yet prove on the prototype
2024-06-02 Add files via upload
    Updated inventor parts
    [Barra_principal.ipt, Petal.ipt, cilindre.ipt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]
2024-06-02 Create Mechanical schematics
2024-06-02 Updated drawings plant parts
    [Barra_principal_planol.dwg, Braç_stepper_plànol.dwg, Calze_plànol.dwg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]
2024-06-02 Last final code
    Not yet tested on the prototype
2024-06-03 Update README.md
    Lastest schematic
2024-06-03 Correct schematic
